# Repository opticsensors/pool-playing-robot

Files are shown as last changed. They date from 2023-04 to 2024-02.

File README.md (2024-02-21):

# `pool-paying-robot`

Design and implementation of a robot that plays the game of pool autonomously. To achieve this goal, three different branches had to be explored:
- **Vision system**: hardware and computer vision algorithms used for detecting and identifying pool balls
- **Shot selection**: algorithms to find the *best* shot given the balls configuration and pool table dimensions
- **Actuation system**: how to send commands to the actuators and the mechanical parts to make the execution of pool shots possible

## 1. Getting started

Run the following command for clonning the repository from GitHub:

```shell
git clone https://github.com/opticsensors/pool-playing-robot.git
```

Then:

1. Make sure  you have the latest version of pip and PyPA’s build installed:
   ```shell
   py -m pip install --upgrade pip
   py -m pip install --upgrade build
   ```

2. In your terminal, navigate to your new project, and initialise Git
   ```shell
   git init
   ```

3. Install the necessary packages using `pip`:
   ```shell
   py -m build
   py -m pip install -e .
   ```

4. Stage all your project files, and make your first commit
   ```shell
   git add .
   git commit -m "First commit"
   ```

## 2. Directory structure
The project follows this tree structure:

```
├── README.md                   <- The top-level README for developers using this project.
├── data                        <- Camera matrix, lens parameters, pool table corners, CNN weights ...
├── cad                         <- CAD files of the pool playing robot parts and the pool table. 
├── arduino                     <- Controls two stepper motors for positioning tasks, with options 
│                                  for homing, microstepping, and activating a solenoid.
│               
├── examples                    <- Python scripts.
│               
├── pyproject.toml              <- Makes project pip installable so src can be imported.               
│                                  The requirements are listed here.
│                
├── src                         <- Source code of this project.
│   └── pool            
│       └── __init__.py         <- Makes pool a Python module that can be imported from everywhere.
│       └── ball_detection.py   <- Computer vision algorithm for detecting pool balls.
│       └── brain.py            <- Analytic solution of 4 types of pool shots.
│       └── calibration.py      <- camera calibration and inverse kinematics of the robot.
│       └── cam.py              <- Controls a DSLR camera using digiCamControl's command line interface.
│       └── dynamixel.py        <- Interacts with the Dynamixel servomotors.
│       └── error_analysis.py   <- Finds the error due to the vision and actuation system
│       └── eye.py              <- Corrects camera lens distortion and adjusts the perspective. 
│       └── pool_env.py         <- Defines a custom environment for simulating a pool game.
│       └── pool_frame.py       <- Creates pool table dimansions and geometry
│       └── pool_sim.py         <- Simulates the physics of a pool game using the Pymunk library.
│       └── random_balls.py     <- Generates random pool ball positions.
│       └── shot_selection.py   <- Chooses what pool shot to play based on the ball positions.
│       └── stepper.py          <- Interacts with the Arduino to send commands to the stepper motors.
│       └── utils.py            <- Contains several system parameters and basic functions.
│
└── LICENSE.txt

```

## 3. Geometry of a pool shot

For the target ball `T` to pass through point `P`, the center of the pocket, the cue ball `C` must strike point `X`. 

Key measures:
- Cut angle: &gamma;
- Cue ball angle: &theta;
- Cue ball impact point: X 

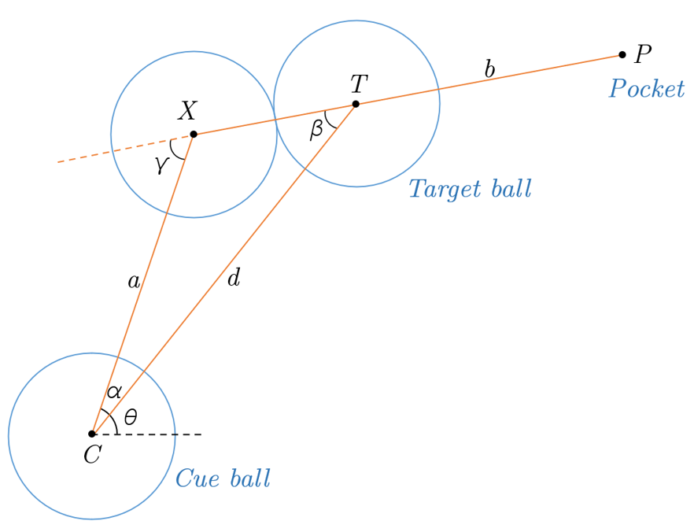
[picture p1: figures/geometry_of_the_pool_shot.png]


## 4. Error analysis

- **Objective**: determine the necessary resolution of the vision and actuation system
- **Simulation**: two ball cut shots that include a unique error via uniform sampling
- **Results**: analyze data with density plots to estimate success probability of sinking a ball

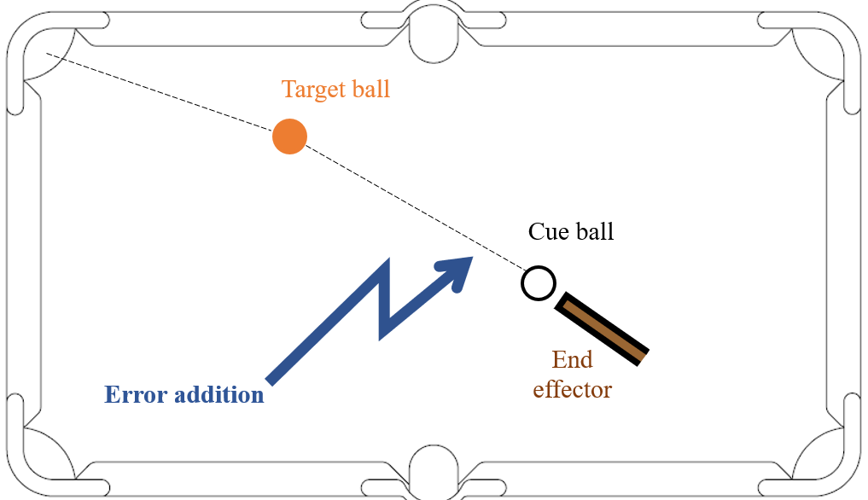
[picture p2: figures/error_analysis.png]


- **Actuation system**: the resolution is expressed as a range of angles from which the cue ball can be propelled. 

- **Vision system**: the resolution is defined by an uncertainty radius within which the predicted centers of the balls may vary. 

In both scenarios, the deviation of the target ball is quantified by the delta error (see image below):

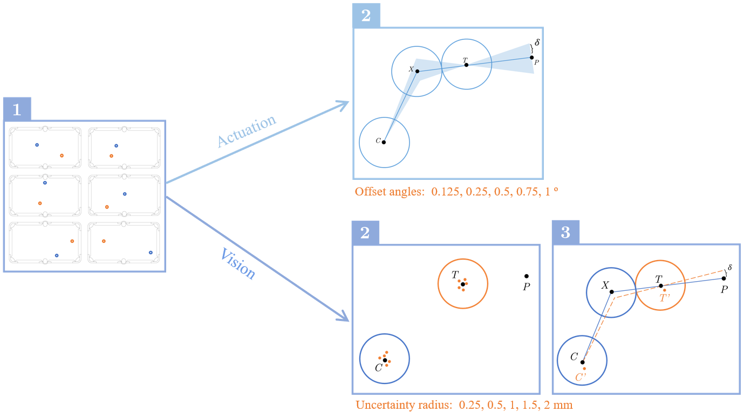
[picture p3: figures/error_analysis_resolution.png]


Analyzing the data from the simulation reveals that the cut angle has a significant effect on the delta error, particularly when this angle is bigger tha 60º, the error increases exponentially. This is why the density plots have been studied separately according to the cut angle.

<table>
  <tr>
    <th>Scatter plot</th>
    <th colspan="4">Density plot</th>
  </tr>
  <tr>
    <th>&delta; vs &gamma;</th>
    <th>0 ≤ γ ≤ 90 </th>
    <th>0 ≤ γ ≤ 30 </th>
    <th>30 ≤ γ ≤ 60</th>
    <th>60 ≤ γ ≤ 90</th>
  </tr>
  <tr>
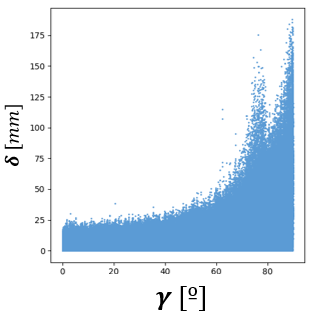
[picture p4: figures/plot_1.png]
    <td></td>
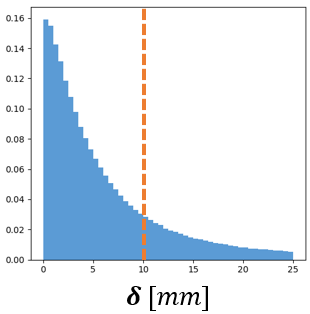
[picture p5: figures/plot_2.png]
    <td></td>
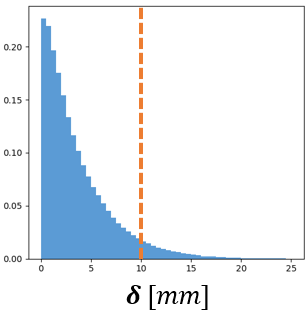
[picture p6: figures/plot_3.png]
    <td></td>
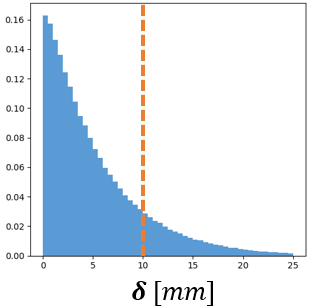
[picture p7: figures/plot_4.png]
    <td></td>
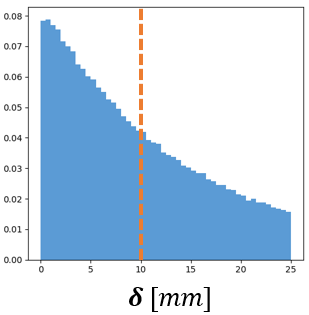
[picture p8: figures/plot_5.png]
    <td></td>
  </tr>
</table>

To calculate the probability of a ball being potted, one must compute the area under the curve of these diagrams between 0 and 10 mm of delta error, since the pockets approximately have a radius of 10 mm. Doing this for each of the resolutions studied, the results as a function of the cut angle are as shown in the tables. A glance at the probability values has led to the decision that the resolution of the vision system should be 0.5 mm or less, and that of the actuation system should be 0.25º or less.

<table>
  <tr>
    <th colspan="5">Probability results for different vision system resolutions </th>
  </tr>
  <tr>
    <th>Resolution</th>
    <th>0 ≤ γ ≤ 90</th>
    <th>0 ≤ γ ≤ 30</th>
    <th>30 ≤ γ ≤ 60</th>
    <th>60 ≤ γ ≤ 90</th>
  </tr>
  <tr>
    <td>0.25 mm</td>
    <td>0.86</td>
    <td>0.98</td>
    <td>0.93</td>
    <td>0.67</td>
  </tr>
  <tr>
    <td>0.5 mm</td>
    <td>0.80</td>
    <td>0.94</td>
    <td>0.84</td>
    <td>0.60</td>
  </tr>
  <tr>
    <td>1 mm</td>
    <td>0.73</td>
    <td>0.85</td>
    <td>0.75</td>
    <td>0.54</td>
  </tr>
  <tr>
    <td>1.5 mm</td>
    <td>0.68</td>
    <td>0.80</td>
    <td>0.69</td>
    <td>0.52</td>
  </tr>
  <tr>
    <td>2 mm</td>
    <td>0.66</td>
    <td>0.76</td>
    <td>0.65</td>
    <td>0.50</td>
  </tr>
</table>

<table>
  <tr>
    <th colspan="5">Probability results for different actuation system resolutions </th>
  </tr>
  <tr>
    <th>Resolution</th>
    <th>0 ≤ γ ≤ 90</th>
    <th>0 ≤ γ ≤ 30</th>
    <th>30 ≤ γ ≤ 60</th>
    <th>60 ≤ γ ≤ 90</th>
  </tr>
  <tr>
    <td>0.125°</td>
    <td>0.87</td>
    <td>0.99</td>
    <td>0.93</td>
    <td>0.66</td>
  </tr>
  <tr>
    <td>0.25°</td>
    <td>0.74</td>
    <td>0.87</td>
    <td>0.75</td>
    <td>0.58</td>
  </tr>
  <tr>
    <td>0.5°</td>
    <td>0.62</td>
    <td>0.72</td>
    <td>0.63</td>
    <td>0.45</td>
  </tr>
  <tr>
    <td>0.75°</td>
    <td>0.56</td>
    <td>0.62</td>
    <td>0.55</td>
    <td>0.45</td>
  </tr>
  <tr>
    <td>1°</td>
    <td>0.48</td>
    <td>0.53</td>
    <td>0.48</td>
    <td>0.38</td>
  </tr>
</table>

## 5. Vision system

### 5.1 Hardware

The hardware includes both the camera and its mounting support. The final setup is shown here:

| Top view | Side view |
|:---:|:---:|
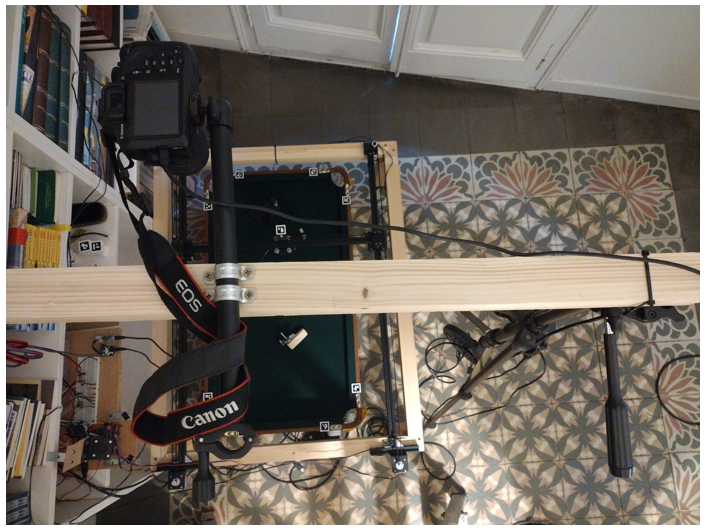
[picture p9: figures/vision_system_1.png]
Top view
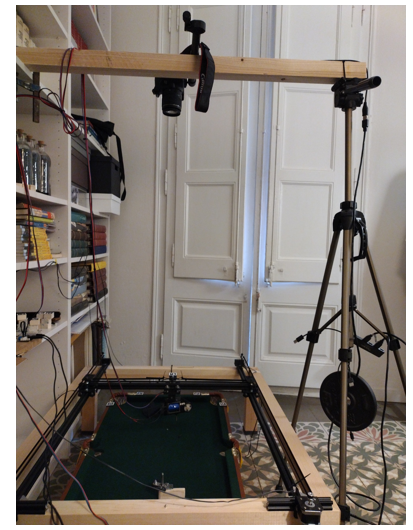
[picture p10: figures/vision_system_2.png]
Side view
|  |  |

To select the right camera, I conducted a resolution test on four different cameras I had at home: a smartphone camera, a Raspberry Pi camera, a DSLR, and a webcam. Based on the results and ease of connectivity with a PC, the final selection was the DSLR camera:

<table>
  <tr>
    <th>Camera</th>
    <td>Samsing A71</td>
    <td>PiCamera</td>
    <td>Canon EOS 1300D</td>
    <td>Logitech c922</td>
  </tr>

  <tr>
    <th>Resolution</th>
    <td>0.28 mm/px</td>
    <td>0.50 mm/px</td>
    <td>0.25 mm/px</td>
    <td>0.50 mm/px</td>
  </tr>

  <tr>
    <th>USAF test</th>
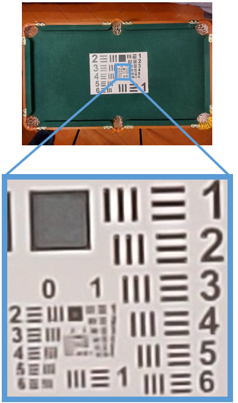
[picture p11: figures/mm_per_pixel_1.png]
    <td>
</td>
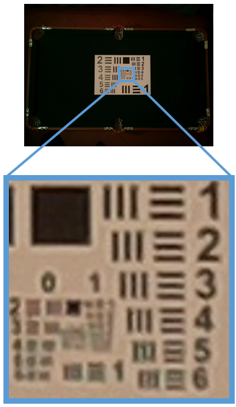
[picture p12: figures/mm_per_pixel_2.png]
    <td>
</td>
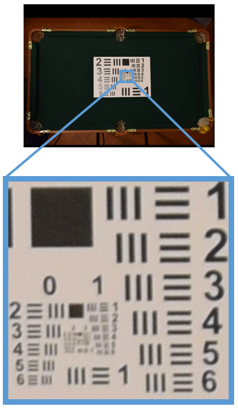
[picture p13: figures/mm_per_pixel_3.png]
    <td>
</td>
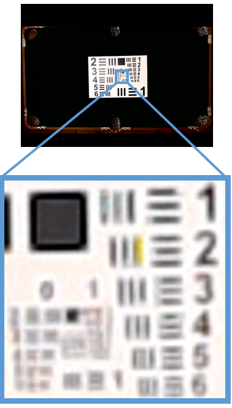
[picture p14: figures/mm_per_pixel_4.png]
    <td>
</td>
  </tr>

</table>

### 5.2 Software

#### 5.2.1 Preprocessing

- **Lens correction**: prevents straight lines from appearing curved.

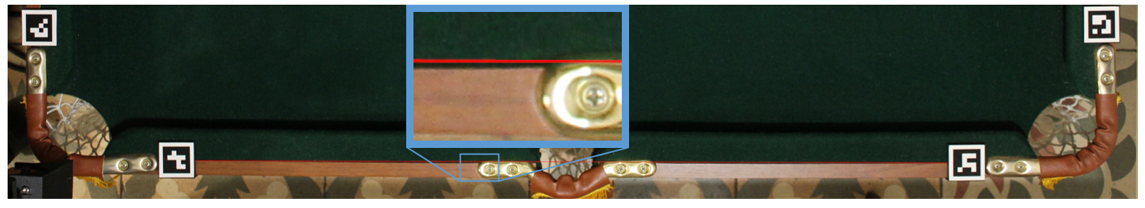
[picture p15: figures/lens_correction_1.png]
| **Before** |  |
|---|---|
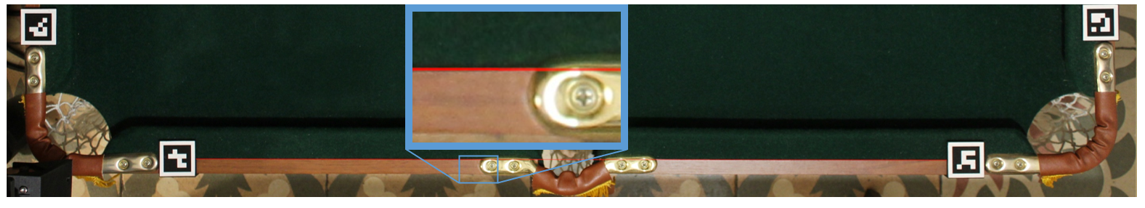
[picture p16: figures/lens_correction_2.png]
| **After** |  |

- **Homography**: Transforms the image so that its corners align with those of the pool table.

| Before | After |
|---|---|
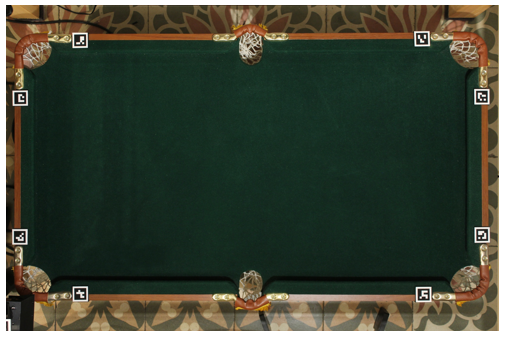
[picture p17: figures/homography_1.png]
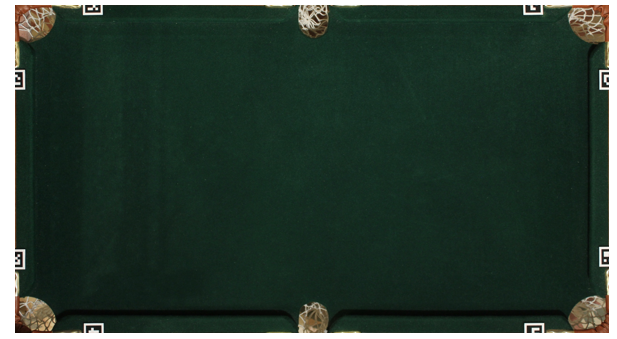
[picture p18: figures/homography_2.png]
|  |  |

- **Camera calibration**: Computes the intrinsic camera parameters using images of a checkerborad pattern.

| Image 1 | Image 2 | Image 3 | Image 4 |
|:-----:|:-----:|:---:|:---:|
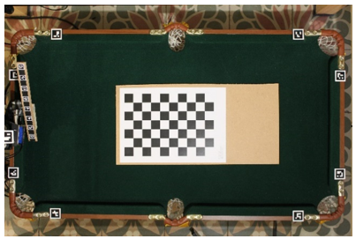
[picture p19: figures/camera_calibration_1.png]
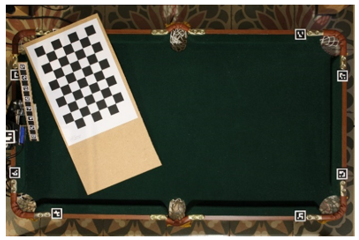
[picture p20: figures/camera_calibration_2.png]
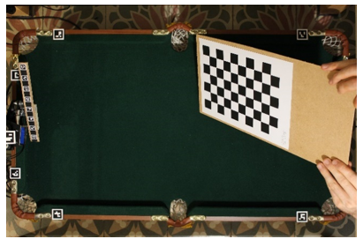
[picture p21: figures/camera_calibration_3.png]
|  |  |  | [...]

#### 5.2.2 YOLOv8

This approach uses the YOLO (version 8 by Ultralytics) detection algorithm, where the image is processed through a CNN, resulting in predictions in the form of rectangles.

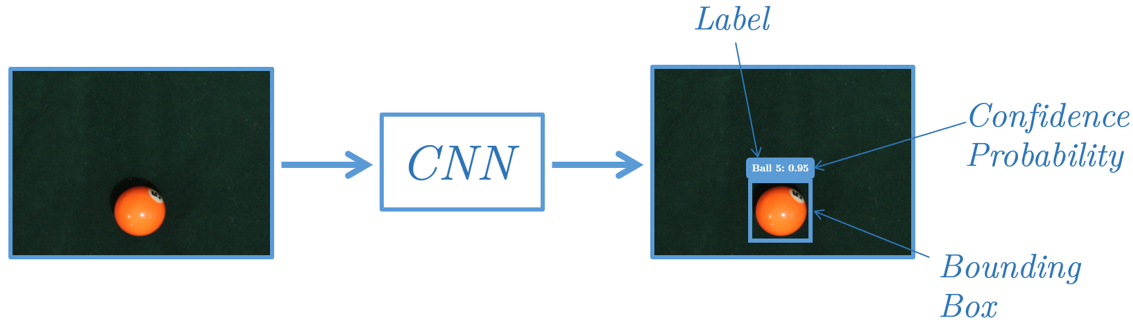
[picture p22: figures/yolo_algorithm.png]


#### 5.2.3 Classic approach

This method employs a set of classic computer vision techniques: color segmentation, morphological operations, the watershed algorithm and color transformation. 

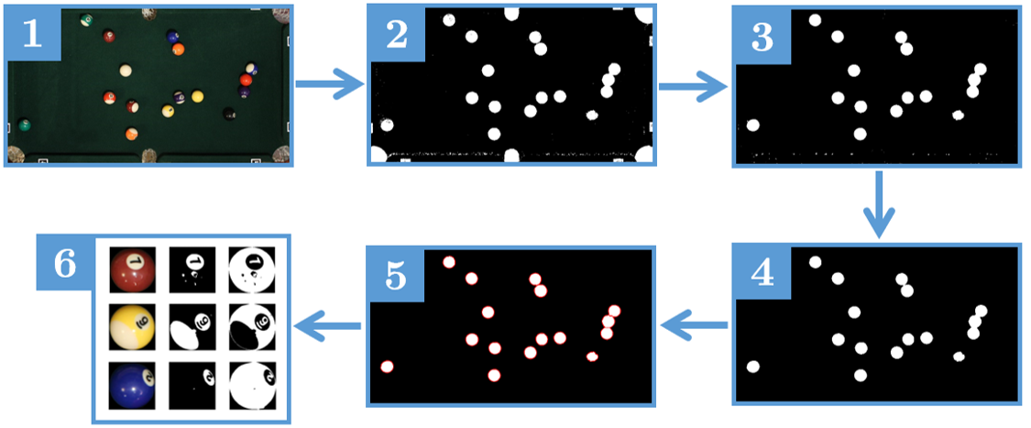
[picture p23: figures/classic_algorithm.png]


#### 5.2.4 Comparison of the results

After comparing the results of both methods against a Ground Truth established by me, it was observed that the classic method is more accurate, but less robust in situations where the balls are very close to each other. 

| Original | Ground truth | Classic | YOLOv8 |
|---|---|---|---|
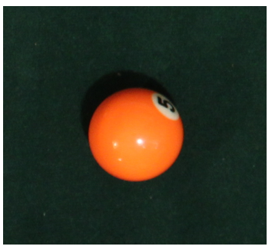
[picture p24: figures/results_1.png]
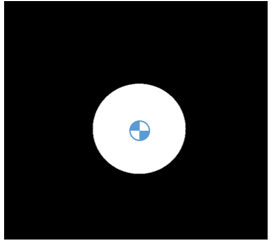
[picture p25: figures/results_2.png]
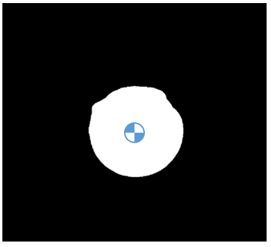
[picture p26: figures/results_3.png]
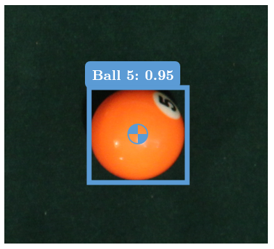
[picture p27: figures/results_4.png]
YOLOv8
|  |  |  |  |

| Algorithm | &mu; [px] | &sigma; [px] |
|---|---|---|
| YOLO | 3.02 | 3.17 |
| Classic | 2.43 | 1.81 |

If the 68–95–99.7 rule is applied, from these results it can be deduced that in 95% of the cases an error below 6.3 and 3.6 pixels should be expected for the YOLO and classic algorithms, respectively. Considering a resolution of 0.25 mm/px, this is 1.5 and 0.9 mm, respectively.

<details><summary><b>Results</b></summary>

Detection of pool balls grouped closely together

| Classic | YOLO |
|---|---|
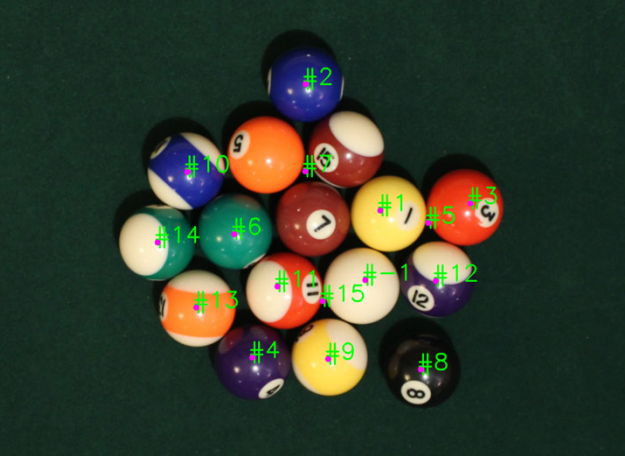
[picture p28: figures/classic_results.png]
Classic
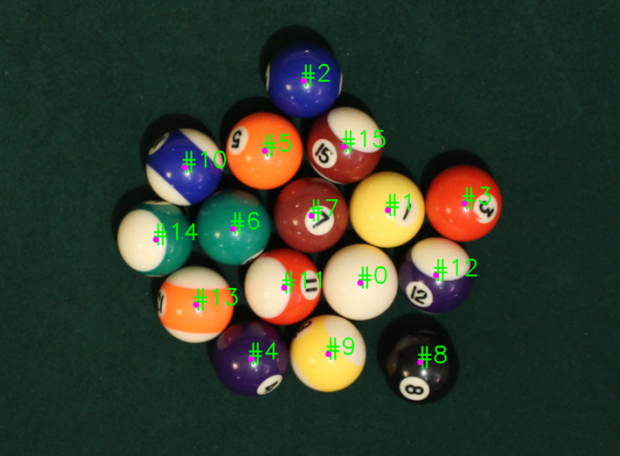
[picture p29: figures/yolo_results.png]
YOLO
|  |  |

</details>

## 6. Shot selection 

### 6.1 Analytic method

- **Pool table geometry simplification**: to simplify the computation of rebounds.

| Original | Simplified |
|---|---|
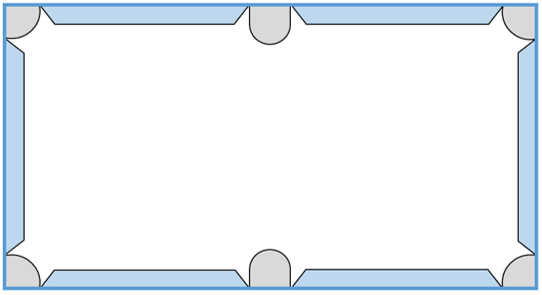
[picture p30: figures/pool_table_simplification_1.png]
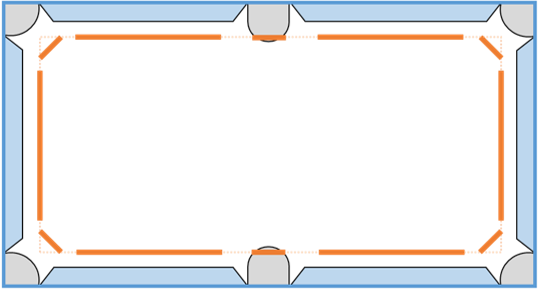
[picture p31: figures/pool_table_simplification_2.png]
|  |  |

- **Compute all possible and impossible shots**: combinations of all the different balls and pockets.

| CTP | CTTP | CBTP | CTBP |
|---|---|---|---|
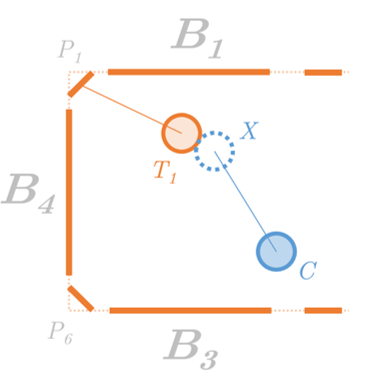
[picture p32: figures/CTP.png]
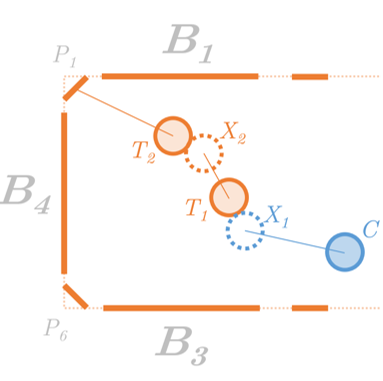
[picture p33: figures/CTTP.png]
CTTP
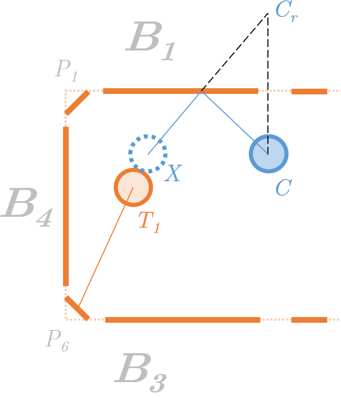
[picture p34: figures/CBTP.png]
CBTP
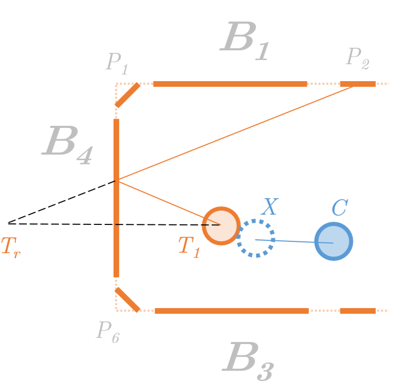
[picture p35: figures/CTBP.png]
CTBP
|  |  |  |  |

- **Filter feasible shots**: collision check using the geometric definition of the cross and dot products.

| No collision | Collision |
|:---:|:---:|
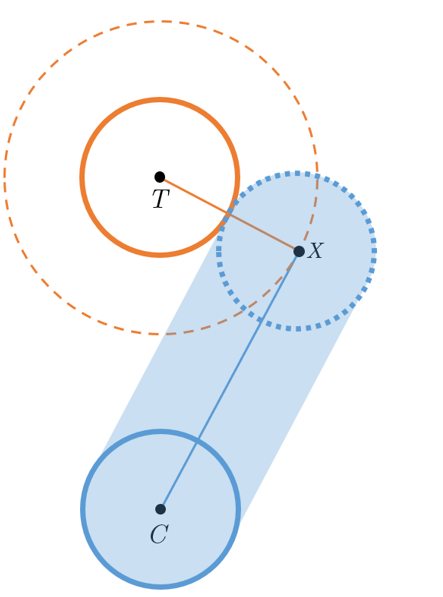
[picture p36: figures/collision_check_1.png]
No collision
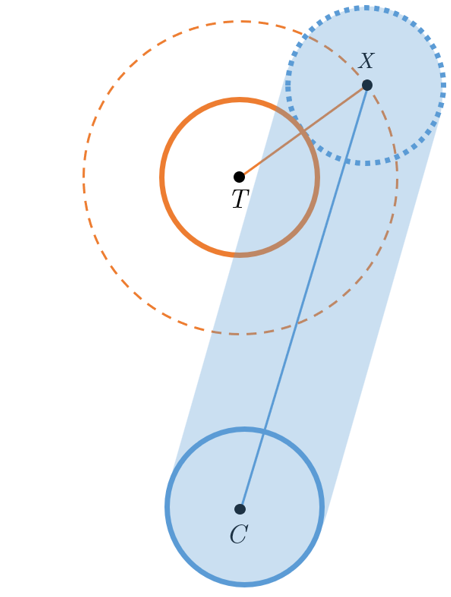
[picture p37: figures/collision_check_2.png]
Collision
|  |  |

- **Choosing the easiest shot**: difficulty metric (using the nomenclature defined above)

$$
\text{difficulty} = \frac{ab}{\cos^2 \gamma}
$$

<details><summary><b>Results</b></summary>

| CTP | CTTP | CBTP | CTBP |
|---|---|---|---|
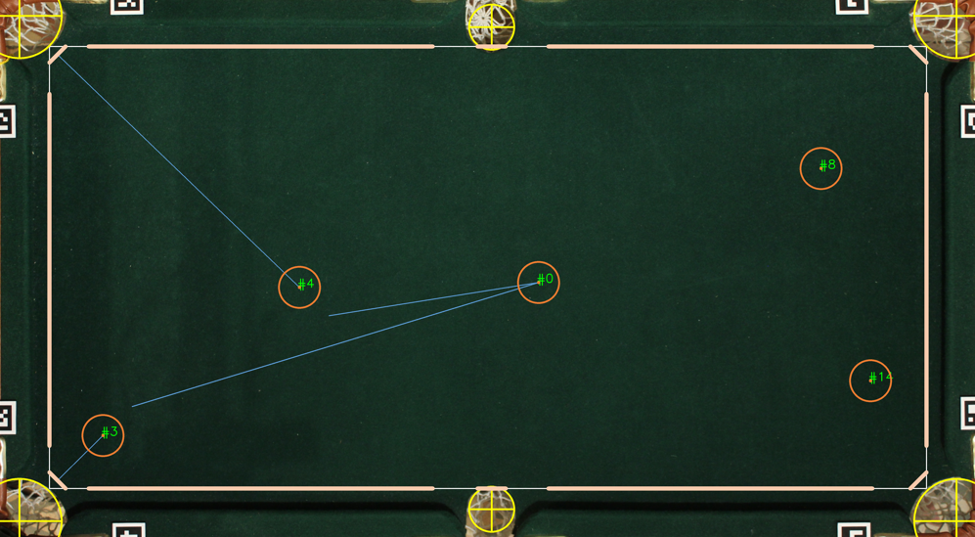
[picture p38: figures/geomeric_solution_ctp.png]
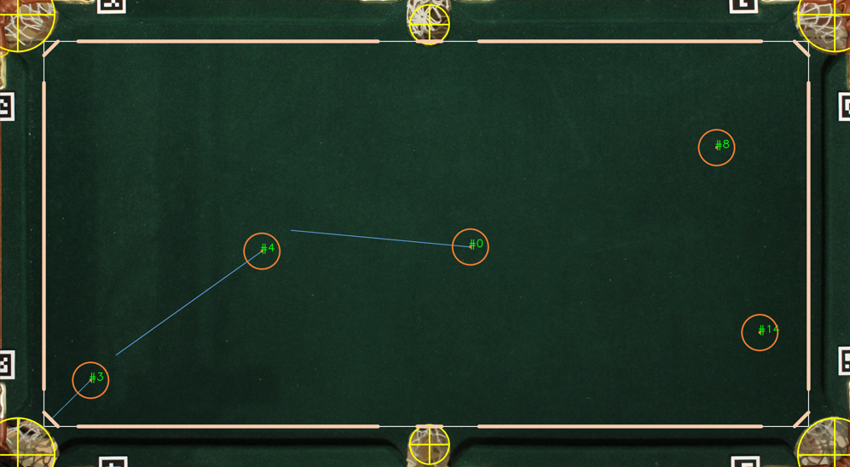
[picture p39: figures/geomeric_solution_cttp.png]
CTTP
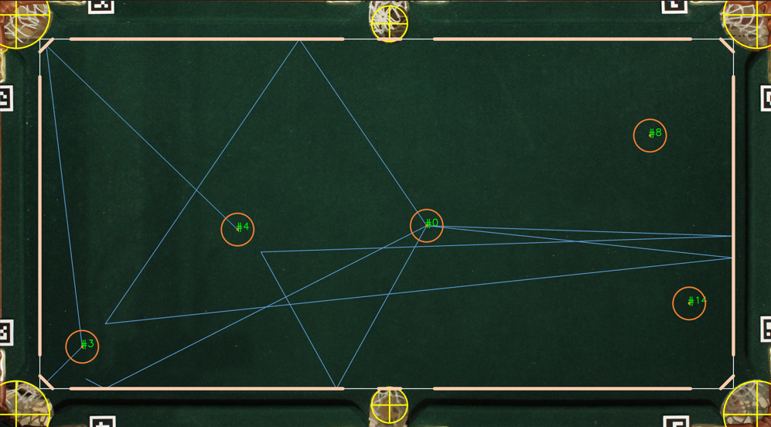
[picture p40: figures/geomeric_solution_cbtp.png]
CBTP
|  |  |  | CTBP |

</details>

### 6.2 Simulation method

- **2D simulation & render**: Pymunk, Pygame
- **Brute force**: every angle is simulated (incr. 0.1º)
- **Easiest shot**: less sensitive angle



## 7. Actuation system: 

The pool robot is divided in 2 subsystems:

- **Cue ball impact**: linear actuator
   - Solenoid
   - Servomotor
- **Cue positioning**: cartesian robot
   - Stepper motors
   - V-slot 2020 and wheels
   - Tooth belt and timing pulleys 

Block diagram of the actuation system showing selected components and
interactions:



- **Homing position**: it's necessary to have a reference position known as home since the stepper motors do not have a way to know their position. This position has been obtained using two limit switches activated by the robot's own moving parts:

<table>
  <tr>
    <th>SolidWorks</th>
    <th>Constructed</th>
  </tr>
  <tr>
    <td rowspan="2">SolidWorks
</td>
    <td>Constructed</td>
  </tr>
  <tr>
    <td>Constructed</td>
  </tr>
</table>

- **Timing belt and pulleys**: the belt has been designed with an H configuration which has allowed the motors to be stationary

<table>
  <tr>
    <th>Concept design H-bot</th>
    <th>Constructed</th>
  </tr>
  <tr>
    <td rowspan="2">SolidWorks
</td>
    <td>Constructed</td>
  </tr>
  <tr>
    <td>Constructed</td>
  </tr>
</table>

- **Belt tensioning and stepper sizing**: a set of pulleys was assembled and the belt was tensioned with zip ties. To achieve this the motors were sized with a calculation of the required torque, considering the accelaration and load terms, and a safety factor

| Belt tensioning | Stepper mount |
|---|---|
| Before | After |

### 7.1 Fliper design:

- **Why a flipper mechanism was developed?**: Because it requires one less degree of freedom, hence, on less motor.

| 2 DOF | 1 DOF |
|:---:|:---:|
| 2 DOF | 1 DOF |

- **Iterative design process**: The first iteration was entirely made with 3D-printed parts and served to test the viability of the concept. This proved successful, leading to a second iteration where the piece was modified to integrate a component from a pinball machine, in order to make it more robust. The final step involved rotating the flipper relative to the Cartesian robot's carriage. To accomplish this, a servo motor was coupled between the two parts.

| Proof of concept | Pinball parts | Servo integration |
|:-----:|:-----:|:---:|
| 2 DOF | 2 DOF | 2 DOF |

- **Solenoid stroke and spring**:  the solenoid's stroke was limited using a screw, and the flipper's return to the retracted position was achieved with a spring.

Stroke                       |            Spring
:-------------------------:|:-------------------------:
|  

### 7.2 Flipper parts:

- **Linkage kinematics simulation**: to obtain the dimensions of the mechanism, its kinematics have been simulated for many possible configurations, and the one that met a series of requirements was selected. For example, ensuring that the flipper, when retracted, does not collide with any balls that might be on the table.

- **Flipper assembly**: to secure the wooden flipper to the steel shaft, Araldite was used, while the shaft was joined to the metal part through welding. 

Flipper assembly           |            Flipper parts
:-------------------------:|:-------------------------:
|  

### 7.3 Control and communications: 

- **Stepper motor**:
   - Accelstepper library
   - Pulse control: steps and direction
   - Stepper driver: DRV8825
   
- **Servomotor**:
   - Dynamixel library: address writing 
   - Trapezoidal velocity profile
   - PID angular position

- **Solenoid**:
   - Logic MOSFET circuit

- **PC interface**:
   - Arduino: serial communication 
   - USB communication converter 

### 7.4 Final prototype:

The cartesian robot is supported by a wooden frame, and the flipper is held in place thanks to the sliding wheel element of the central bar, which is inverted.

SolidWorks                      |            Constructed
:-------------------------:|:-------------------------:
|  

## 8. System integration

Find relationship between:

- Outputs from the vision system: cue ball pixel coordinates `uc`, `vc`
- Outputs from the shot selection algorithm: cue ball trajectory angle &theta;
- Commands to be sent to the stepper motors: `q1`, `q2`; and the servomotor: `q3`

### 8.1 Robot kinematics

- **Cartesian robot kinematics**: relationship between the stepper motors' rotational movement and the linear displacement of the carriage. 

Stepper rotation vs. carriage movement   |            Steps vs. distance
:-------------------------:|:-------------------------:
|  

- **Evaluating flipper positioning**: The flipper has an offset relative to the axis of rotation.

| Initial condition | Flipper rotation | Flipper translation |
|:-----:|:-----:|:---:|
| Initial condition | Flipper rotation | Flipper translation |

It was deduced that:

- The cue ball's position in pixels (`uc`, `vc`), and the cosine and sine of the flipper's angle (&theta;), have a linear relationship with the steps of the motors (`q1`, `q2`). 

- The flipper's angle (&theta;) directly corresponds to the position we need to set the servo motor to (`q3`).

### 8.2 Calibration procedure

A calibration process was developed to experimentally determine the robot's inverse. This process involves:

1. Move the carriage to six predetermined known positions. 
2. For each of these positions, the servo motor must be moved to a random angle.
3. Place an Aruco marker directly under the flipper, simulating where the cue ball would be located.

| Predefined grid of points | Aruco under the flipper  | Final Aruco positions |
|:-----:|:-----:|:---:|
| Predefined grid of points | Aruco under the flipper | Final Aruco positions |

By using the information from the Aruco markers' positions (`uc`, `vc`), as well as the positions of the carriage and the servo motor (`X_C`, `Y_C`, &theta;), a dataset can be created. This dataset allows for the adjustment of a linear regression model between the desired variables.

$$
X_c = A \cos \theta + B \sin \theta + C u_c + D v_c + E
$$

$$
Y_c = F \cos \theta + G \sin \theta + H u_c + I v_c + J
$$

After computing the linear regression coefficients, the required motor steps can be determined via the inverse kinematics:

$$
\begin{bmatrix} q_1 \\\ q_2 \end{bmatrix} = 1/\lambda \begin{bmatrix} -1/2 & 1/2\\\ 1/2 & 1/2\end{bmatrix} \begin{bmatrix} X_C \\\ Y_C \end{bmatrix}
$$

## 9. Results 

20 cut shots (for cut angle less than 45º):
 - 15 out of 20 successful shots (75% success rate)
 - Cue ball trajectory: 
   - Average deviation of 0.65º
   - Standard deviation of 0.4º (max deviation of 1.2º)

| Shot 1 |  Shot 2 |  Shot 3 |  Shot 4 |
|---|---|---|---|
| Shot 1 | Shot 2 | Shot 3 | Shot 4 |

The results were obtained using video analysis of the cue ball trajectory:
- Camera: smartphone top down view
- Ball tracking: MOG
- Cue path angle: GIMP

Top down view                      |            MOG results
:-------------------------:|:-------------------------:
|

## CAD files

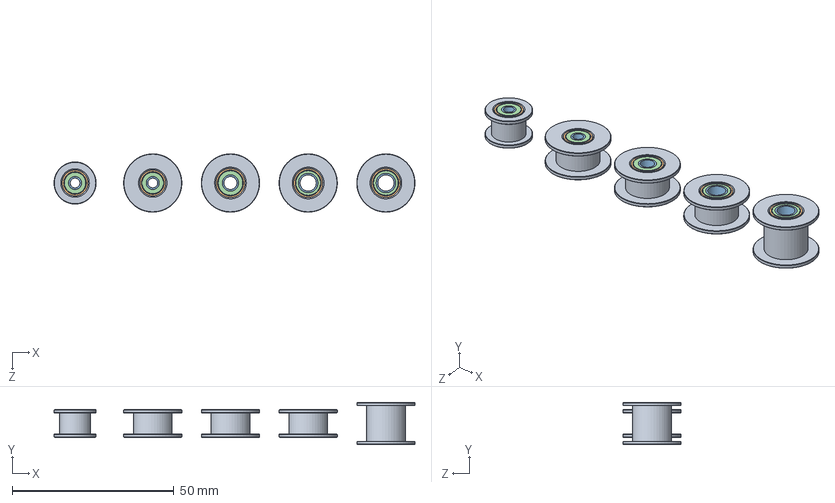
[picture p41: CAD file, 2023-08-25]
cad/solid_works/GT2 Idler Pulley, Configurable, Pulleys Lined Up in Assembly.SLDASM
111.5 x 13.0 x 18.0 mm
Body, GT2 Idler Pulley, Configurable x 5
Bearing Outer Ring, GT2 Idler Pulley, Configurable x 10
Bearing Inner Ring, GT2 Idler Pulley, Configurable x 10
Bearing Seal, GT2 Idler Pulley, Configurable x 20
Bearing Ball, GT2 Idler Pulley, Configurable x 88

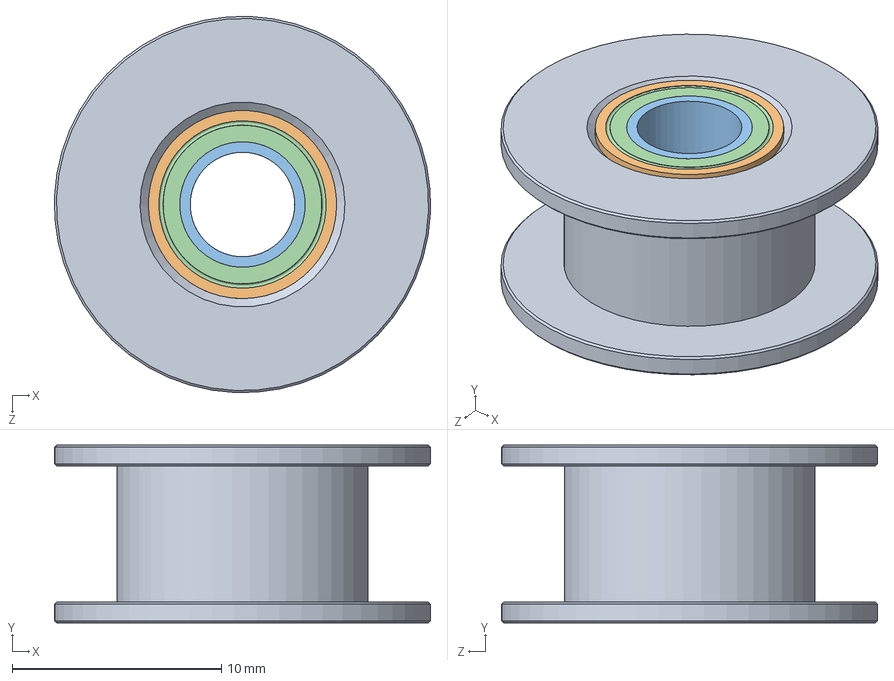
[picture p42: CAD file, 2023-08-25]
cad/solid_works/GT2 Idler Pulley, Configurable.SLDASM
18.0 x 8.50 x 18.0 mm
Body, GT2 Idler Pulley, Configurable
Bearing Outer Ring, GT2 Idler Pulley, Configurable x 2
Bearing Inner Ring, GT2 Idler Pulley, Configurable x 2
Bearing Seal, GT2 Idler Pulley, Configurable x 4
Bearing Ball, GT2 Idler Pulley, Configurable x 24

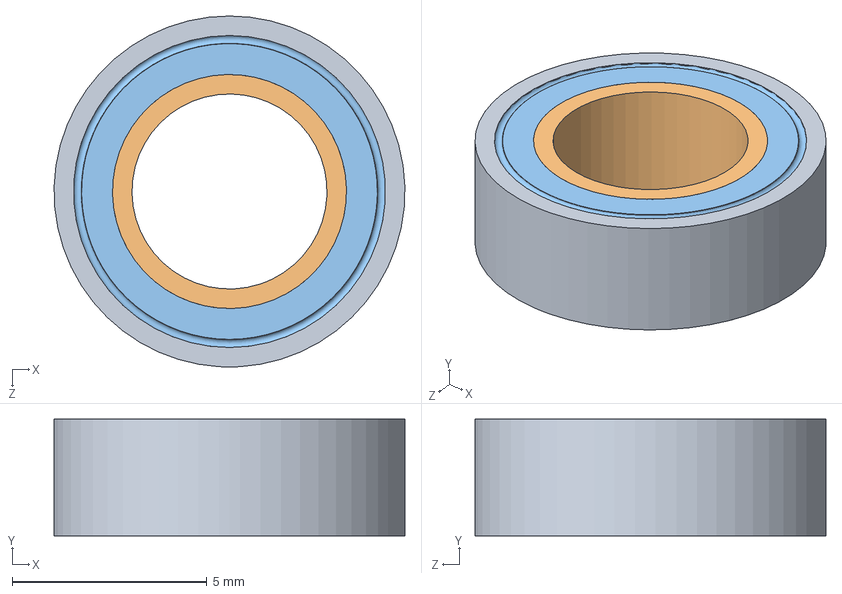
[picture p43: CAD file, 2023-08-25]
cad/solid_works/Bearing Subassy, GT2 Idler Pulley, Configurable.SLDASM
9.00 x 3.00 x 9.00 mm
Bearing Outer Ring, GT2 Idler Pulley, Configurable
Bearing Inner Ring, GT2 Idler Pulley, Configurable
Bearing Seal, GT2 Idler Pulley, Configurable x 2
Bearing Ball, GT2 Idler Pulley, Configurable x 12

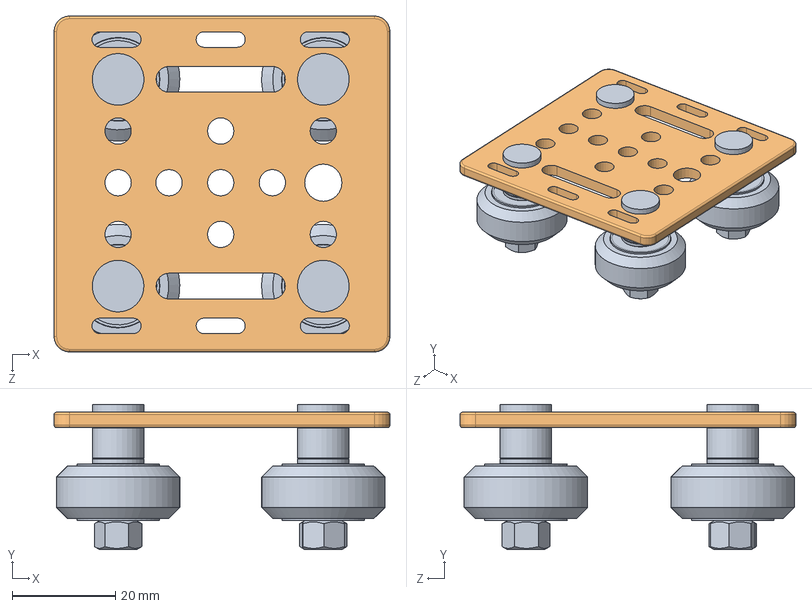
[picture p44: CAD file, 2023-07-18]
cad/solid_works/v wheels + plate.SLDASM
65.0 x 28.1 x 65.0 mm
v wheel x 4
v wheel plate v2

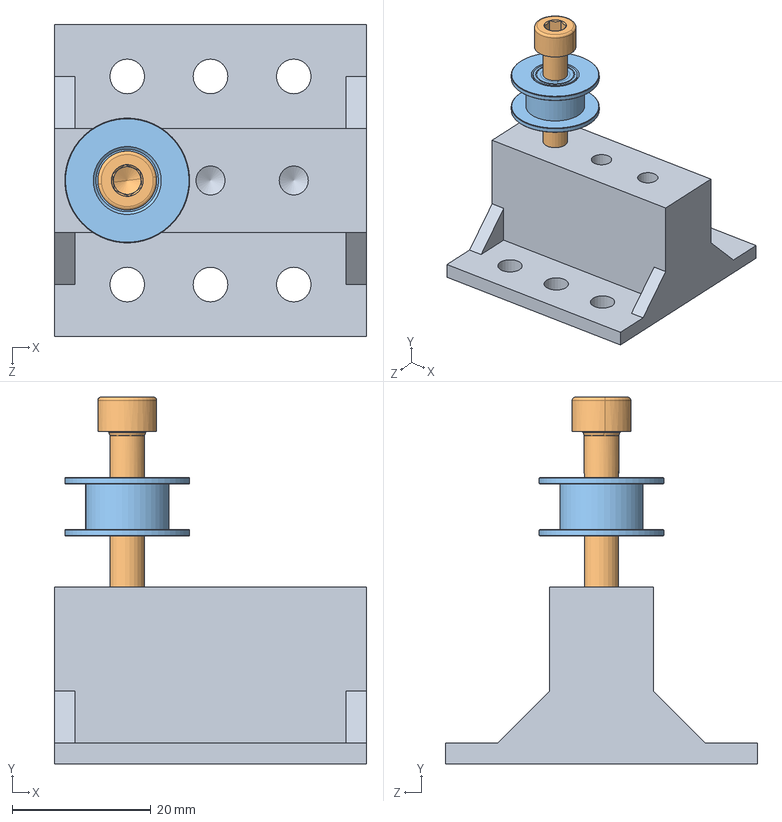
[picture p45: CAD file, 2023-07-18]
cad/solid_works/single idler pulley support.SLDASM
45.0 x 52.9 x 45.0 mm
single idler pulley support
m5 allen screw 40mm
GT2 Idler Pulley

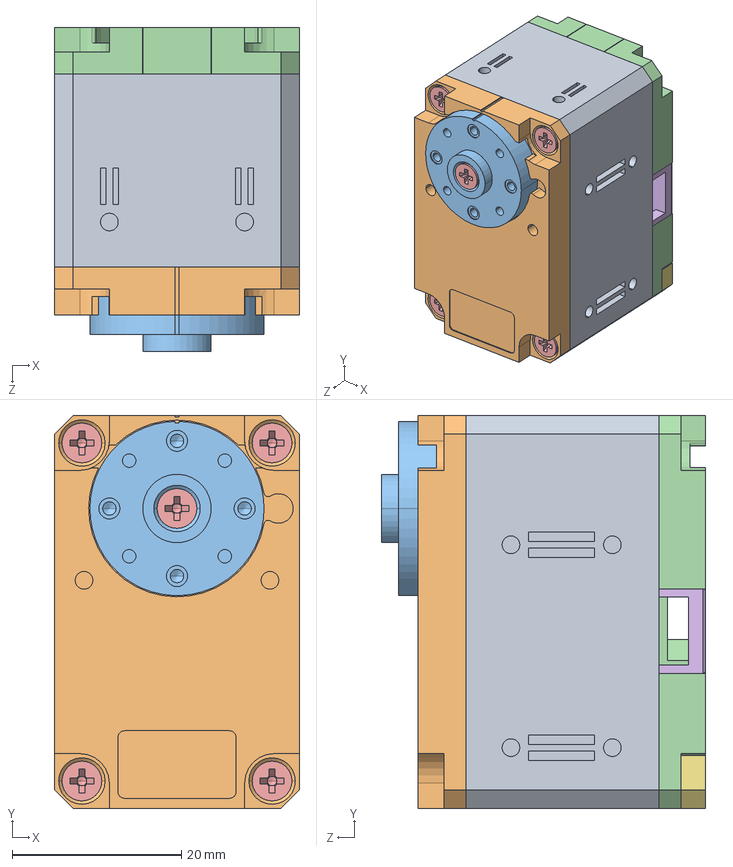
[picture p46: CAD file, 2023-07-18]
cad/solid_works/XL430_W250_T.SLDASM
29.0 x 46.5 x 38.3 mm
Part1^XL430_W250_T.STEP
Part2^XL430_W250_T.STEP
Part3^XL430_W250_T.STEP
Part4^XL430_W250_T.STEP
countersunk flat head cross recess screw_din_DIN EN ISO 7046-1 - M2.5 x 10 - Z - 10N.STEP x 9
Part5^XL430_W250_T.STEP
Part6^XL430_W250_T.STEP

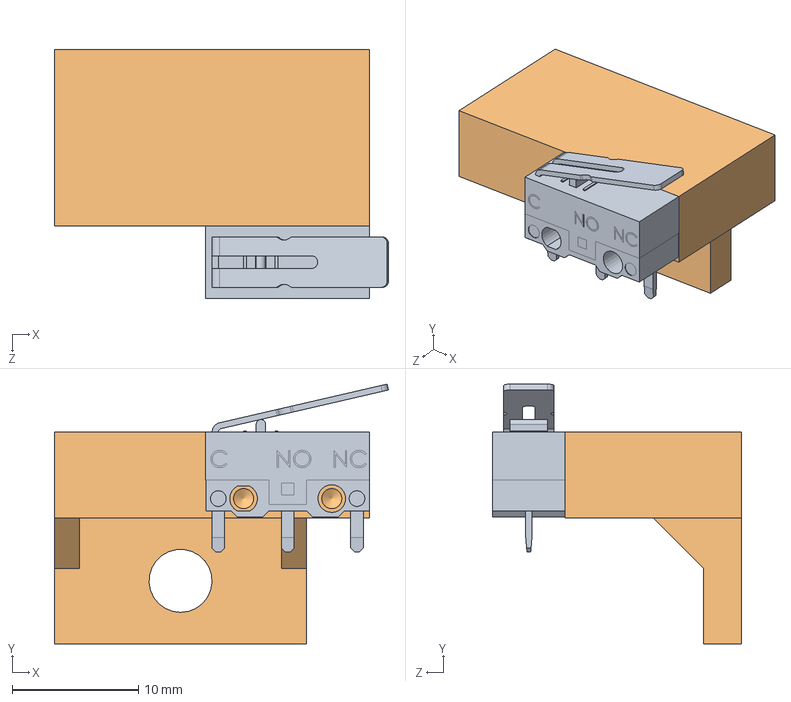
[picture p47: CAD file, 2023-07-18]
cad/solid_works/Limit_Switch_assembly.SLDASM
26.5 x 20.6 x 19.8 mm
Limit_Switch
limit_switch_support v3

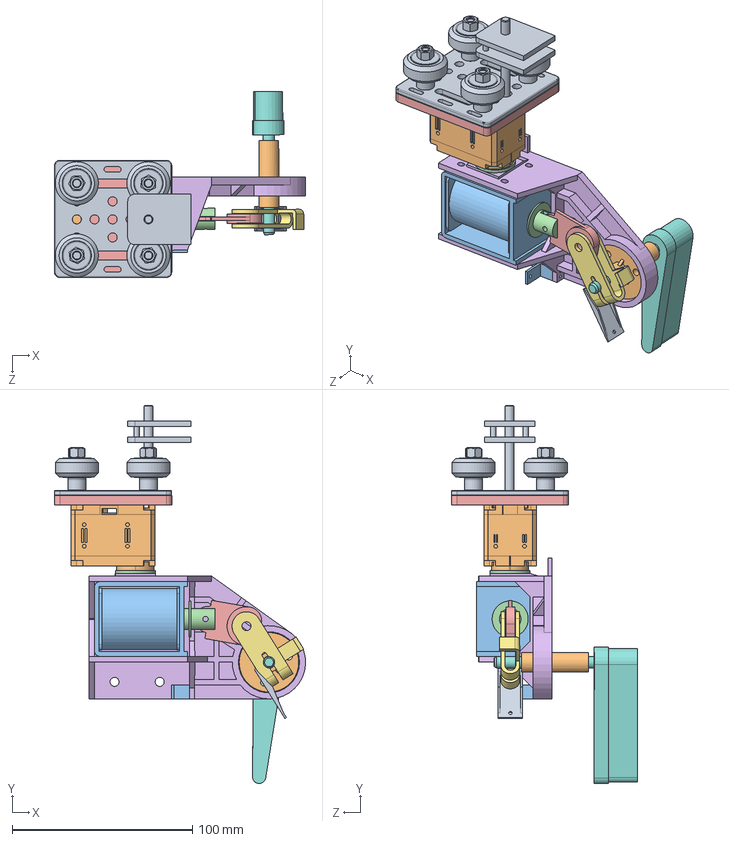
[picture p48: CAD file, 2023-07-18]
cad/solid_works/Actuator.SLDASM
139.2 x 209.5 x 103.1 mm
v wheels + plate central
XL430_W250_T
Heshchen_solenoid
Heshchen_plungger
l1_link
case x 2
l2_link_v2
flipper
tensioner_holder
axis_support
spring_holdder
dynamixel_spacer
dynamixel_support

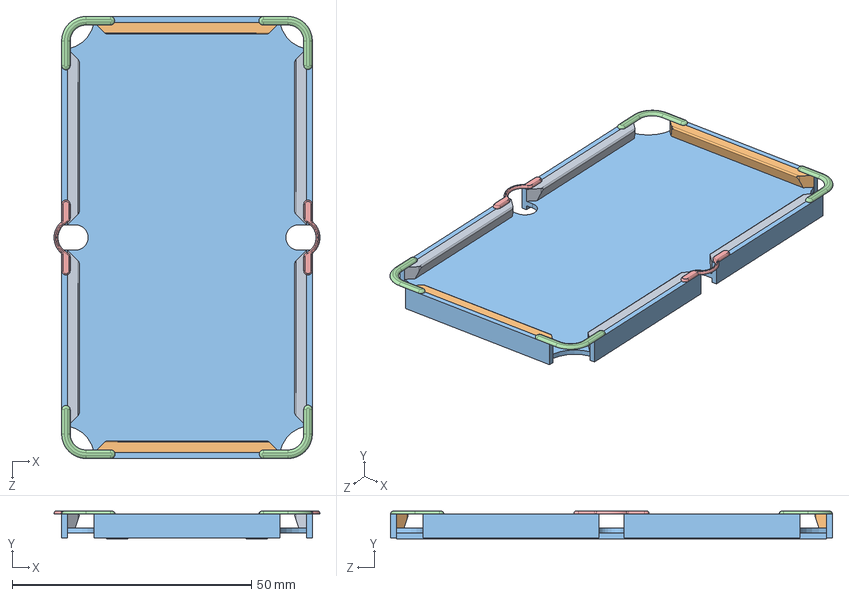
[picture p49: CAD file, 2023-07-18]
cad/solid_works/billar.SLDASM
55.6 x 5.84 x 92.4 mm
borde_corto x 4
borde_largo x 2
mesa
corner_strap x 4
middle_straps x 2

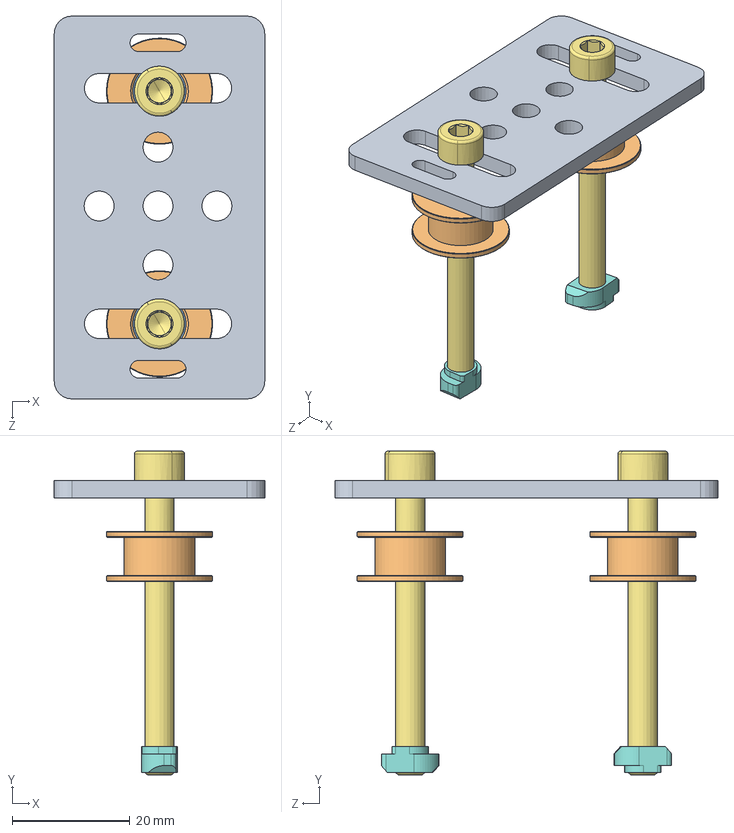
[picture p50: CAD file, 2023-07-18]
cad/solid_works/idler pulley support.SLDASM
35.7 x 55.0 x 65.0 mm
idler pulley plate
Body, GT2 Idler Pulley, Configurable x 2
Bearing Outer Ring, GT2 Idler Pulley, Configurable x 4
Bearing Inner Ring, GT2 Idler Pulley, Configurable x 4
Bearing Seal, GT2 Idler Pulley, Configurable x 8
Bearing Ball, GT2 Idler Pulley, Configurable x 48
m5 allen screw x 2
M5_T_Slot nut x 2

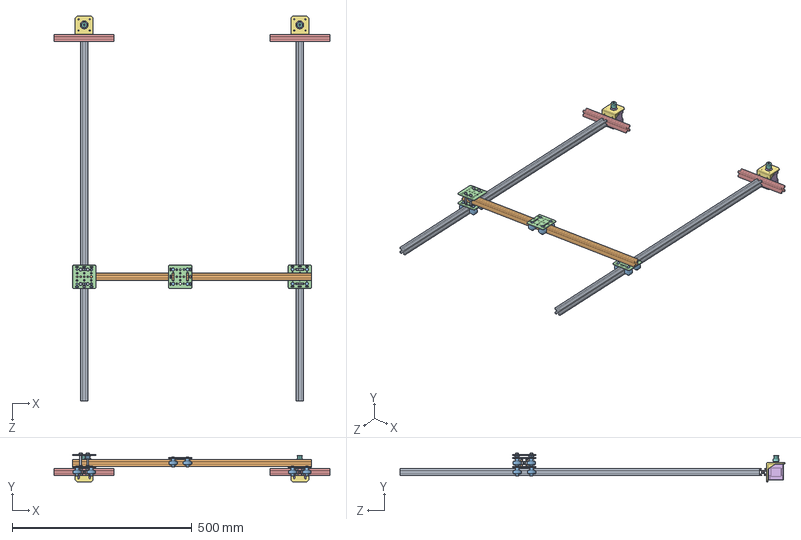
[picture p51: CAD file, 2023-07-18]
cad/solid_works/cartesian_robot.SLDASM
767.0 x 80.4 x 1071.5 mm
v slot 2020 1000mm x 2
v slot 2020 666mm
v wheel x 12
v wheel plate x 4
v slot 2020 167mm x 2
NEMA 17 x 2
Stepper Motor Mount NEMA_17 Sized x 2
2GT 20B5 x 2
formed hex screw_am x 4
hex nut jam_am x 4
GT2 Timing Idler Pulley x 2

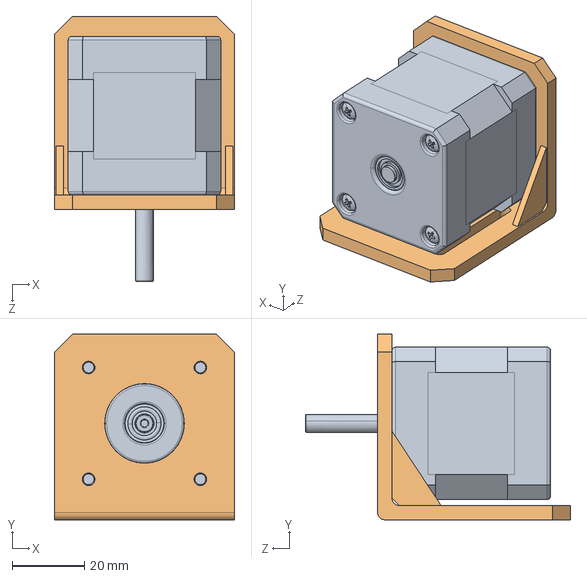
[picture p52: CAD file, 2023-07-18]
cad/solid_works/NEMA 17 + support.SLDASM
50.0 x 51.5 x 73.5 mm
NEMA 17
Stepper Motor Mount NEMA_17 Sized

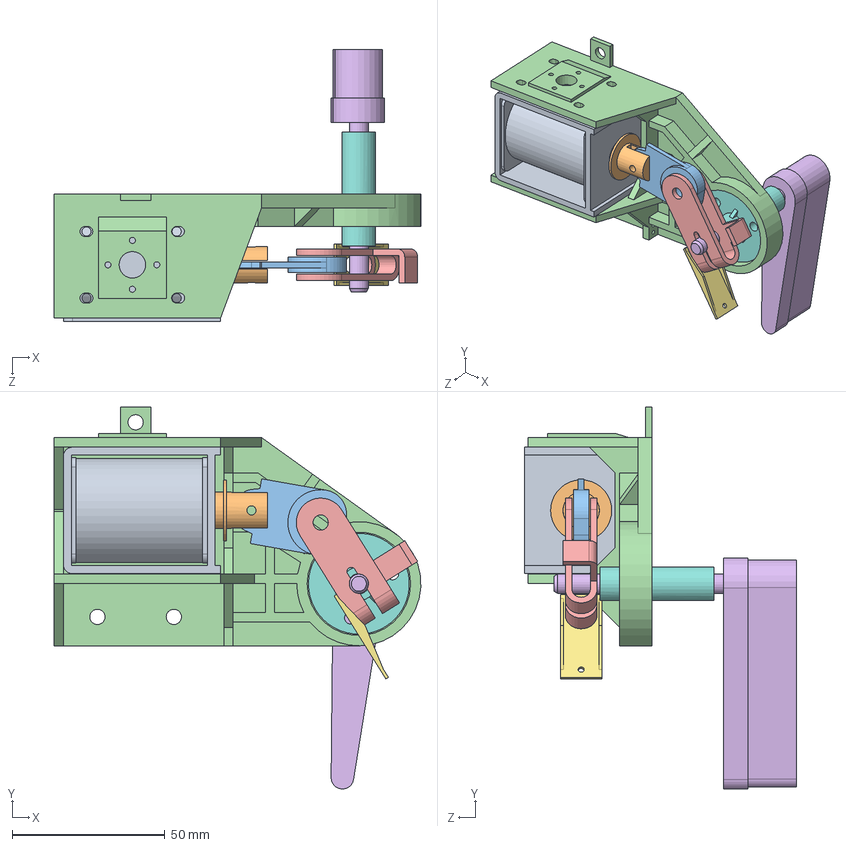
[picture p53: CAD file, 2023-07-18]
cad/solid_works/my_pinball_flipper_design.SLDASM
120.0 x 125.0 x 89.1 mm
Heshchen_solenoid
Heshchen_plungger
l1_link
case
l2_link_v2
flipper
tensioner_holder
axis_support

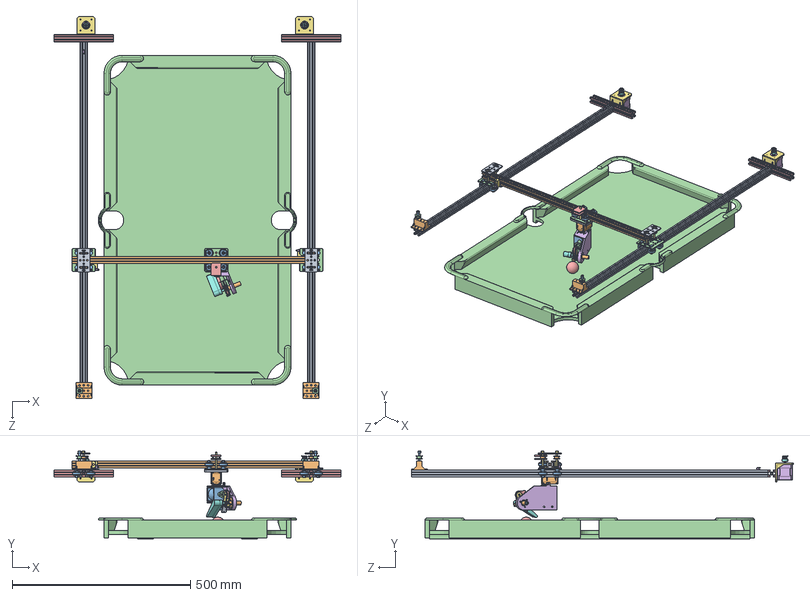
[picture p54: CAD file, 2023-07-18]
cad/solid_works/my final design.SLDASM
804.0 x 246.1 x 1071.5 mm
v slot 2020 1000mm x 2
v slot 2020 666mm
v wheel x 12
v wheel plate v2 x 3
v slot 2020 167mm x 2
NEMA 17 x 2
Stepper Motor Mount NEMA_17 Sized x 2
2GT 20B5 x 2
idler pulley plate x 4
Body, GT2 Idler Pulley, Configurable x 8
Bearing Outer Ring, GT2 Idler Pulley, Configurable x 16
Bearing Inner Ring, GT2 Idler Pulley, Configurable x 16
Bearing Seal, GT2 Idler Pulley, Configurable x 32
Bearing Ball, GT2 Idler Pulley, Configurable x 192
m5 allen screw x 9
M5_T_Slot nut x 8
hex nut style 1_am x 8
single idler pulley support x 4
m5 allen screw 40mm x 4
GT2 Idler Pulley x 4
belt tensioner
Limit_Switch x 3
limit_switch_support v3 x 2
dynamixel_spacer
dynamixel_support
XL430_W250_T
Heshchen_solenoid
Heshchen_plungger
l1_link
case
l2_link_v2
flipper
tensioner_holder
axis_support
spring_holdder
billar scaled
bola

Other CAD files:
cad/solid_works/SimetríaLimit_Switch_assembly.SLDASM
cad/solid_works/GT2 Idler Pulley.SLDASM
cad/solid_works/v wheels + plate central.SLDASM
cad/solid_works/cartesian_robot v4.SLDASM
cad/solid_works/2GT 20B5.SLDPRT
cad/solid_works/Bearing Ball, GT2 Idler Pulley, Configurable.SLDPRT
cad/solid_works/Bearing Inner Ring, GT2 Idler Pulley, Configurable.SLDPRT
cad/solid_works/Bearing Outer Ring, GT2 Idler Pulley, Configurable.SLDPRT
cad/solid_works/Bearing Seal, GT2 Idler Pulley, Configurable.SLDPRT
cad/solid_works/Body, GT2 Idler Pulley, Configurable.SLDPRT
cad/solid_works/GT2 Idler Pulley with teeth.SLDPRT
cad/solid_works/GT2 Idler Pulley.SLDPRT
cad/solid_works/Heshchen_plungger.SLDPRT
cad/solid_works/Heshchen_solenoid.SLDPRT
cad/solid_works/Limit_Switch.SLDPRT
cad/solid_works/M5_T_Slot nut.SLDPRT
cad/solid_works/NEMA 17 + support.SLDPRT
cad/solid_works/NEMA 17.SLDPRT
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

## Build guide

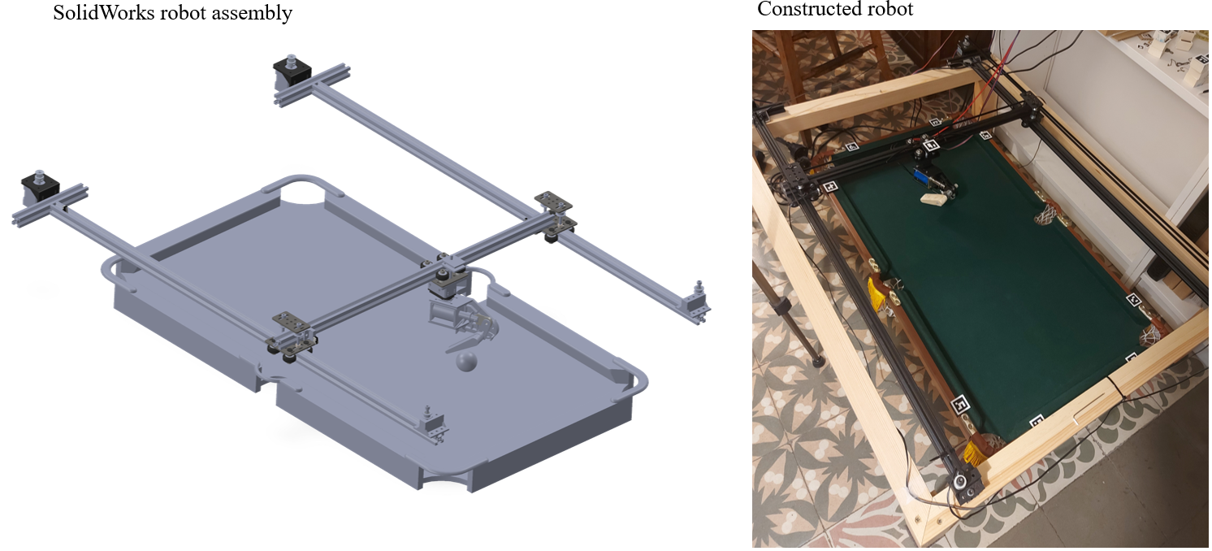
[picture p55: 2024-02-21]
figures/final_assembly.png

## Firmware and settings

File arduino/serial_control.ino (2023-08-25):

//Libraries to include
#include <AccelStepper.h>

//stepper control outputs
#define mot1StepPin 6
#define mot1DirPin 3
#define mot2StepPin 5
#define mot2DirPin 2
#define motMS1Pin 7
#define motMS2Pin 8
#define motMS3Pin 9
#define topSwitch 10
#define bottomSwitch 12
#define leftSwitch 11
#define rightSwitch 13
#define solenoidPin 4

// Define the stepper motor and the pins that is connected to
AccelStepper stepper1(1, mot1StepPin, mot1DirPin); // (Typeof driver: with 2 pins, STEP, DIR)
AccelStepper stepper2(1, mot2StepPin, mot2DirPin);

// Define velocities and accelerations
int calibrationVelocity = 500;
int calibrationAcceleration = 1000;
int workingVelocity = 500;
int workingAcceleration = 1000;

// variables to store calibration positions
int reach_position1;
int reach_position2;

const byte numChars = 64;
char receivedChars[numChars];
char tempChars[numChars];        // temporary array for use when parsing
int sign1 = 1;
int sign2 = 1;
int backup_position = 300;
int infinity = 32766;
int untilTheEnd1 = 0;
int untilTheEnd2 = 0;

boolean newData = false;

// variables to hold the parsed data
int relative_position_stepper1 = 0;
int relative_position_stepper2 = 0;
int mode = -1;
byte microSteps[6] = {
    B000, // full step
    B100, // half step
    B010, // 1/4 step
    B110, // 1/8 step
    B001, // 1/16 step
    B101, // 1/32 step
};

//===============

void setup() {

    Serial.begin(9600);

    // configure initial motor settings
    pinMode(motMS1Pin, OUTPUT);
    pinMode(motMS2Pin, OUTPUT);
    pinMode(motMS3Pin, OUTPUT);

    pinMode(topSwitch, INPUT_PULLUP);
    pinMode(bottomSwitch, INPUT_PULLUP);
    pinMode(leftSwitch, INPUT_PULLUP);
    pinMode(rightSwitch, INPUT_PULLUP);

    pinMode(solenoidPin, OUTPUT);

    digitalWrite(motMS1Pin, LOW);
    digitalWrite(motMS2Pin, LOW);
    digitalWrite(motMS3Pin, LOW);

    delay(200);
    setSpeedAccel(workingVelocity, workingAcceleration);
    Serial.println("<Arduino is ready>");

}

//===============

void loop() {
    recvWithStartEndMarkers();
    
    // every time new data comes, we set the current position of the motors to 0 steps
    // this is because we will move the motors with visual servoing (error vector)
    stepper1.setCurrentPosition(0); 
    stepper2.setCurrentPosition(0);

    if (newData == true) {
        strcpy(tempChars, receivedChars);
            // this temporary copy is necessary to protect the original data
            //   because strtok() used in parseData() replaces the commas with \0
        parseData();
        
        // step mode (includes microstepping option)
        if (mode >= 0) {
            digitalWrite(motMS1Pin, bitRead(microSteps[mode], 2));
            digitalWrite(motMS2Pin, bitRead(microSteps[mode], 1));
            digitalWrite(motMS3Pin, bitRead(microSteps[mode], 0));
            moveSafe();
        }

        // homing
        else if (mode == -1) {
            delay(5000);
            setSpeedAccel(calibrationVelocity, calibrationAcceleration);
            homing();
            setSpeedAccel(workingVelocity, workingAcceleration);
        }

        // calibration mode (find corners)
        else if (mode == -2) {
            delay(5000);
            setSpeedAccel(calibrationVelocity, calibrationAcceleration);
            findMaxPositions();
            setSpeedAccel(workingVelocity, workingAcceleration);
        }

        else if (mode == -3) {
            digitalWrite(solenoidPin, HIGH);      //Switch Solenoid ON
            delay(230);                          //Wait 
            digitalWrite(solenoidPin, LOW);       //Switch Solenoid OFF
            delay(1000); 
        }

    replyToPython();

    }
}

//===============

void setSpeedAccel(int speed, int accel){
    stepper1.setMaxSpeed(speed); // Set maximum speed value for the stepper
    stepper1.setAcceleration(accel); // Set acceleration value for the stepper
    stepper2.setMaxSpeed(speed);
    stepper2.setAcceleration(accel);
}

void positionSigns(int pin){

    // when we touch a limit switch, we need to back off a little bit until 
    // it stops being pressed. For this reason, negative values on limit  
    // switched pins are considered  

    if (pin==leftSwitch || pin==-rightSwitch) {
        sign1=-1;  
        sign2=-1;  
    }
    else if (pin==rightSwitch || pin==-leftSwitch) {
        sign1=1;  
        sign2=1;
    }
    else if (pin==topSwitch || pin==-bottomSwitch) {
        sign1=1;  
        sign2=-1;
    }
    else if (pin==bottomSwitch || pin==-topSwitch) {
        sign1=-1;  
        sign2=1;
    }
}

void reachEnd(int pin) {
    untilTheEnd1=0;
    untilTheEnd2=0;
    stepper1.setCurrentPosition(0);  // Set the current position as zero for now
    stepper2.setCurrentPosition(0);  // Set the current position as zero for now
    positionSigns( pin );
    delay(200);

    stepper1.moveTo(sign1*infinity);  // Set the position to move to
    stepper2.moveTo(sign2*infinity);  // Set the position to move to
    while (digitalRead(pin)) {  // Make the Stepper move CCW until the switch is activated   
        stepper1.run();  // Start moving the stepper
        stepper2.run();  // Start moving the stepper
        untilTheEnd1=untilTheEnd1+sign1;
        untilTheEnd2=untilTheEnd2+sign2;

    }
    stepper1.stop(); // Stop as fast as possible
    stepper2.stop(); // Stop as fast as possible  

    stepper1.setCurrentPosition(0);  // Set the current position as zero for now
    stepper2.setCurrentPosition(0);  // Set the current position as zero for now
    positionSigns( -pin );
    delay(200);

    stepper1.moveTo(sign1*backup_position);  // Set the position to move to
    stepper2.moveTo(sign2*backup_position);  // Set the position to move to
    while (stepper1.currentPosition() != sign1*backup_position || stepper2.currentPosition() != sign2*backup_position) { // Make the Stepper move CW until the switch is deactivated
        stepper1.run();
        stepper2.run();
        untilTheEnd1=untilTheEnd1+sign1;
        untilTheEnd2=untilTheEnd2+sign2;
    }
    
    stepper1.setCurrentPosition(0);  // Set the current position as zero for now
    stepper2.setCurrentPosition(0);  // Set the current position as zero for now
    delay(200);

}

void homing() {

    reachEnd(leftSwitch);
    reachEnd(topSwitch);

    relative_position_stepper1 = 0;
    relative_position_stepper2 = 0;

}

void findMaxPositions() {

    reachEnd(rightSwitch);
    relative_position_stepper1=relative_position_stepper1+untilTheEnd1;
    relative_position_stepper2=relative_position_stepper2+untilTheEnd2;

    reachEnd(bottomSwitch);
    relative_position_stepper1=relative_position_stepper1+untilTheEnd1;
    relative_position_stepper2=relative_position_stepper2+untilTheEnd2;
}

void moveSafe() {
    stepper1.moveTo(relative_position_stepper1);
    stepper2.moveTo(relative_position_stepper2);
    // when we achieved the desired position, we exit the while loop
    while (stepper1.currentPosition() != relative_position_stepper1 || stepper2.currentPosition() != relative_position_stepper2 ) {
        // before running we make sure that switches are not pressed
        if (digitalRead(topSwitch) && digitalRead(bottomSwitch) && digitalRead(leftSwitch) && digitalRead(rightSwitch)){
            stepper1.run();  // Move or step the motor implementing accelerations and decelerations to achieve the target position. Non-blocking function
            stepper2.run();
        }

        else{
            stepper1.stop(); // Stop as fast as possible
            stepper2.stop(); // Stop as fast as possible  
            mode=-1;
            homing();
            break;
        }
    }
}

void parseData() {      // split the data into its parts

    char * strtokIndx; // this is used by strtok() as an index
    strtokIndx = strtok(tempChars,",");      // get the first part - the string
    mode = atoi(strtokIndx);     // convert this part to an integer
    strtokIndx = strtok(NULL, ","); // this continues where the previous call left off
    relative_position_stepper1 = atoi(strtokIndx);     // convert this part to an integer
    strtokIndx = strtok(NULL, ","); // this continues where the previous call left off
    relative_position_stepper2 = atoi(strtokIndx);     // convert this part to an integer
}

void recvWithStartEndMarkers() {
    static boolean recvInProgress = false;
    static byte ndx = 0;
    char startMarker = '<';
    char endMarker = '>';
    char rc;

    while (Serial.available() > 0 && newData == false) {
        rc = Serial.read();

        if (recvInProgress == true) {
            if (rc != endMarker) {
                receivedChars[ndx] = rc;
                ndx++;
                if (ndx >= numChars) {
                    ndx = numChars - 1;
                }
            }
            else {
                receivedChars[ndx] = '\0'; // terminate the string
                recvInProgress = false;
                ndx = 0;
                newData = true;
            }
        }

        else if (rc == startMarker) {
            recvInProgress = true;
        }
    }
}

//===============

void replyToPython() {

    Serial.print("<");
    Serial.print(mode);
    Serial.print(",");
    Serial.print(relative_position_stepper1);
    Serial.print(",");
    Serial.print(relative_position_stepper2);
    Serial.print('>');

        // change the state of the data bool everytime a reply is sent
    newData = false;
}

//===============

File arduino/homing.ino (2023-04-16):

// This is very similar to Example 3 - Receive with start- and end-markers
//    in Serial Input Basics   http://forum.arduino.cc/index.php?topic=396450.0

#include <AccelStepper.h>

//stepper control outputs
#define mot1StepPin 6
#define mot1DirPin 3
#define mot2StepPin 5
#define mot2DirPin 2
#define topSwitch 10
#define bottomSwitch 12
#define leftSwitch 11
#define rightSwitch 13

// Define the stepper motor and the pins that is connected to
AccelStepper stepper1(1, mot1StepPin, mot1DirPin); // (Typeof driver: with 2 pins, STEP, DIR)
AccelStepper stepper2(1, mot2StepPin, mot2DirPin);

int initial_homing1 = -1;
int initial_homing2 = -1;

int pos1 = 1500;
int pos2 = 1500;
int time = 0;

int maxTravel1=5000;
int maxTravel2=5000;

//===============

void setup() {

    Serial.begin(9600);

    pinMode(topSwitch, INPUT_PULLUP);
    pinMode(bottomSwitch, INPUT_PULLUP);
    pinMode(leftSwitch, INPUT_PULLUP);
    pinMode(rightSwitch, INPUT_PULLUP);

    delay(200);
    Serial.println("<Arduino is ready>");
    
    //homing();

}

//===============

void loop() {
    homing_v2();
    // every time new data comes, we set the current position of the motors to 0 steps
    // this is because we will move the motors with visual servoing (error vector)
    stepper1.setCurrentPosition(0); 
    stepper2.setCurrentPosition(0);

    stepper1.moveTo(pos1);
    stepper2.moveTo(pos2);
    // when we achieved the desired position, we exit the while loop
    while (stepper1.currentPosition() != pos1 || stepper2.currentPosition() != pos2 ) {
        // before running we make sure that switches are not pressed
        if (digitalRead(topSwitch) && digitalRead(bottomSwitch) && digitalRead(leftSwitch) && digitalRead(rightSwitch)){
            stepper1.run();  // Move or step the motor implementing accelerations and decelerations to achieve the target position. Non-blocking function
            stepper2.run();
        }

    }   

    pos1=-pos1;
    //pos2=-pos2;
    delay(3000);

}

//===============

void homing() {
    stepper1.setMaxSpeed(400); // Set maximum speed value for the stepper
    stepper1.setAcceleration(700); // Set acceleration value for the stepper
    stepper2.setMaxSpeed(400);
    stepper2.setAcceleration(700);

    while (digitalRead(leftSwitch)) {  // Make the Stepper move CCW until the switch is activated   
        stepper1.moveTo(initial_homing1);  // Set the position to move to
        stepper2.moveTo(initial_homing2);  // Set the position to move to
        initial_homing1--;  // Decrease by 1 for next move if needed
        initial_homing2--;  // Decrease by 1 for next move if needed
        stepper1.run();  // Start moving the stepper
        stepper2.run();  // Start moving the stepper
        delay(time);
    }
    Serial.println("left reached");
    stepper1.setCurrentPosition(0);  // Set the current position as zero for now
    stepper2.setCurrentPosition(0);  // Set the current position as zero for now
    initial_homing1=1;
    initial_homing2=1;
    delay(200);

    //while (!digitalRead(leftSwitch)) { // Make the Stepper move CW until the switch is deactivated
    //    stepper1.moveTo(initial_homing1);  // Set the position to move to
    //    stepper2.moveTo(initial_homing2);  // Set the position to move to
    //    stepper1.run();
    //    stepper2.run();
    //    initial_homing1++;
    //    initial_homing2++;
        //delay(5);
    //}
    for (int i = 0; i <= 200; i++) {
        stepper1.moveTo(initial_homing1);  // Set the position to move to
        stepper2.moveTo(initial_homing2);  // Set the position to move to
        initial_homing1++;  // Decrease by 1 for next move if needed
        initial_homing2++;  // Decrease by 1 for next move if needed
        stepper1.run();  // Start moving the stepper
        stepper2.run();  // Start moving the stepper
        //Serial.println(i);
        delay(time);
    }
    stepper1.setCurrentPosition(0);  // Set the current position as zero for now
    stepper2.setCurrentPosition(0);  // Set the current position as zero for now
    initial_homing1=1;
    initial_homing2=-1;
    delay(200);

    while (digitalRead(topSwitch)) {  // Make the Stepper move CCW until the switch is activated   
        stepper1.moveTo(initial_homing1);  // Set the position to move to
        stepper2.moveTo(initial_homing2);  // Set the position to move to
        initial_homing1++;  // Decrease by 1 for next move if needed
        initial_homing2--;  // Decrease by 1 for next move if needed
        stepper1.run();  // Start moving the stepper
        stepper2.run();  // Start moving the stepper
        delay(time);
    }
    Serial.println("top reached");
    stepper1.setCurrentPosition(0);  // Set the current position as zero for now
    stepper2.setCurrentPosition(0);  // Set the current position as zero for now
    initial_homing1=-1;
    initial_homing2=1;
    delay(200);

    //while (!digitalRead(topSwitch)) { // Make the Stepper move CW until the switch is deactivated
    //    stepper1.moveTo(initial_homing1);  // Set the position to move to
    //    stepper2.moveTo(initial_homing2);  // Set the position to move to
    //    initial_homing1--;
    //    initial_homing2++;
    //    stepper1.run();
    //    stepper2.run();
        //delay(5);
    //}
    for (int i = 0; i <= 200; i++) {
        stepper1.moveTo(initial_homing1);  // Set the position to move to
        stepper2.moveTo(initial_homing2);  // Set the position to move to
        initial_homing1--;  // Decrease by 1 for next move if needed
        initial_homing2++;  // Decrease by 1 for next move if needed
        stepper1.run();  // Start moving the stepper
        stepper2.run();  // Start moving the stepper
        //Serial.println(i);
        delay(time);

    }
    stepper1.setMaxSpeed(600); // Set maximum speed value for the stepper
    stepper1.setAcceleration(800); // Set acceleration value for the stepper
    stepper2.setMaxSpeed(600);
    stepper2.setAcceleration(800);
    delay(200);
}
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

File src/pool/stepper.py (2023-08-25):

from typing import *  # type: ignore

import serial
import serial.tools.list_ports


class Stepper(object):
    """Goes in pair with `serial_control.ino`"""

    def __init__(
        self,
        baudRate       : int           = 9600,
        serialPortName : Optional[str] = None
    ):
        self.connected : bool = True

        if serialPortName is None:
            self.connected : bool = False
            self._automatically_connenct_to_arduino()

        self.startMarker     : str           = '<'
        self.endMarker       : str           = '>'
        self.dataStarted     : bool          = False
        self.dataBuf         : str           = ""
        self.messageComplete : bool          = False
        self.baudRate        : int           = baudRate
        self.serialPortName  : Optional[str] = serialPortName

    def _automatically_connenct_to_arduino(self):
        """Connects to the arduino"""

        # get the first port that has "Arduino" in the name
        for port in self._list_com_ports():
            if "Arduino" in port['name']:
                self.serialPortName = port['device']
                self.connected      = True
                break

    @staticmethod
    def _list_com_ports():
        com_ports = serial.tools.list_ports.comports()
        port_list = []
        
        for port in com_ports:
            port_info = {
                'device': port.device,
                'name'  : port.description
            }
            port_list.append(port_info)
        
        return port_list

    def test_if_connected(self) -> bool:
        """Tests if the arduino is connected"""
        return self.connected

    def waitForArduino(self):

        # wait until the Arduino sends 'Arduino is ready' - allows time for Arduino reset
        # it also ensures that any bytes left over from a previous message are discarded
        
        print("Waiting for Arduino to reset")
        
        msg = ""
        while msg.find("Arduino is ready") == -1:
            msg = self.recvLikeArduino()
            if not (msg == 'XXX'): 
                print(msg)

    def setupSerial(self):

        self.serialPort = serial.Serial(port= self.serialPortName, baudrate = self.baudRate, timeout=0, rtscts=True)

        print("Serial port " + self.serialPortName + " opened  Baudrate " + str(self.baudRate))

        self.waitForArduino()

    def sendToArduino(self,stringToSend):
        assert self.connected, "Arduino is not connected"

        stringWithMarkers = (self.startMarker)
        stringWithMarkers += stringToSend
        stringWithMarkers += (self.endMarker)

        self.serialPort.write(stringWithMarkers.encode('utf-8')) # encode needed for Python3

    def recvLikeArduino(self):

        if self.serialPort.inWaiting() > 0 and self.messageComplete == False:
            x = self.serialPort.read().decode("utf-8") # decode needed for Python3
            
            if self.dataStarted == True:
                if x != self.endMarker:
                    self.dataBuf = self.dataBuf + x
                else:
                    self.dataStarted = False
                    self.messageComplete = True
            elif x == self.startMarker:
                self.dataBuf = ''
                self.dataStarted = True
        
        if (self.messageComplete == True):
            self.messageComplete = False
            return self.dataBuf
        else:
            return "XXX" 

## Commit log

2023-03-29 added arduino libraries
2023-03-30 stepper class to replace py_serial.py
    [serial_control.ino, stepper.py]
2023-03-30 added dslr camera support
2023-04-10 minor fixes and modifications
    [serial_control.ino]
2023-04-10 added lens calibration and updated todo
2023-04-12 micro limit switch test
2023-04-12 added new camera sketch
2023-04-12 moved calibration script
2023-04-13 homing and micro limit switch added
2023-04-15 arduino control: homing and calibration
2023-04-16 arduino control enhanced
2023-04-16 working arduino code
2023-04-17 calibration pixels vs steps
2023-04-19 calibration pixel to step
2023-04-20 calibration proccess is working
    [pixel_step.csv]
2023-04-21 debug calibration pixel to steps
2023-04-21 corrected corner order in wwwarp prespective transform
    [eye.py]
2023-04-21 debugger pixel to step worinkg
    [pixel_step.csv]
2023-04-22 model pixel to step and int positions
    [pixel_step.csv]
2023-04-23 updated offline and online calibration data generation
    [calibration_image_data.csv, calibration_pixel_step.csv, calibration_pixel_to_step.csv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]
2023-04-23 deleted a few files that are not necessary
    [calibration_pixel_step.csv]
2023-04-23 working model and data extraction
    [calibration_pixel_to_step.csv]
2023-04-29 repeatability test added 2
    [repeatability_error.csv, repeatability_image_data.csv]
2023-04-29 refactor: Extracted `Camera.settings` to `Camera_settings`
2023-05-01 updated todo and added solenoid sizing script
2023-05-01 feat: Camera controller has `test_if_any_cameras_are_connected`
2023-05-01 refactor: renamed `Stepper` to `Controller_actuators` and improved it
2023-05-01 refactor: Renamed `Camera` to `Camera_DLSR`
    The logic behind this is that in the future we might incorporate a class like `Camera_webcam`
2023-05-01 refactor: Renamed `Camera_settings` and `stepper.py` file
2023-05-04 new script img processing and print added
2023-05-06 feat: Improved `Camera_DLSR` and `sketch_get_corners.py`
2023-05-07 mechanism kinematics
2023-05-09 mechanism kinematics brute force
2023-05-19 dynamixel velocity profile and solenoid serial
2023-05-27 dynamixel dynamics analysis
    [mod_data_0.csv, mod_data_1.csv, mod_data_2.csv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]
2023-05-27 added dynamixel PID tunning
2023-05-30 added pool frame and minor changes
2023-05-31 first brain release and mod pixel to step
    [calibration_image_data.csv, calibration_pixel_to_step.csv]
2023-06-05 working on fourth case shot and mod fin_X method
2023-06-05 fourth case working
2023-06-06 bug in cbtp shot ball #3
    [brain.py, shot_selection.py]
2023-06-06 solved collision bug adding more ids to row match
    [brain.py, shot_selection.py]
2023-06-07 moved X1 and X2 calculations to error analysis
    [brain.py, error_analysis.py]
2023-06-15 bug regarding size obs_space and size state
    [pool_sim.py]
2023-06-15 bug in variable observation space size
    [pool_sim.py]
2023-06-15 solved bug simplifying the problem
    [random_balls.py]
2023-06-19 refactor: changed pool frame pockets
2023-06-20 add: new enviroments and dataset generation
    [pool_sim_data.csv]
2023-06-20 add: new brute force and generation dataset
    [brute_force_data.csv, pool_sim_data_header.csv]
2023-06-21 added: trying machine learning algorithms
    [brute_force_data.csv, pool_sim_data_header.csv]
2023-06-21 bug: wrong info dict potted balls
    [brute_force_data.csv]
2023-06-21 refactor: moved scripts that don't need data to examples
    [brute_force_data.csv, mod_data_0.csv, mod_data_1.csv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]
2023-06-22 refactor: moving sketches to examples and eye class mod
    [calibration_image_data.csv, calibration_pixel_to_step.csv, repeatability_error.csv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]
2023-06-22 refactor: moving sketches to examples
    [calibration_image_data.csv, calibration_pixel_to_step.csv, repeatability_error.csv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]
2023-06-23 corrected X1 and X2 computation and ehanced green region algorithm
    [error_analysis.py]
2023-06-23 checkpoint before error analysis refactor
    [error_analysis.py]
2023-06-24 refactor: vectorized error analysis class
    [error_analysis.py, utils.py]
2023-06-24 refactor: calibration pixels to steps
    [calibration_image_data.csv, calibration_pixel_to_step.csv]
2023-06-28 added system calibration
    [repeatability_error.csv, repeatability_image_data.csv]
2023-06-28 removed ball detection algorithms from eye (imports were too slow)
    [ball_detection.py, eye.py]
2023-06-28 refactor: stepper calibration using DataExtractor class
2023-06-29 modified system calibration
2023-06-30 fix: corrected flipper angle
    [calibration.py]
2023-07-01 added: analytic camera calibration
2023-07-01 added_ tune offset analytic calibration
2023-07-03 added: new cam calibration and regression model
2023-07-04 added: automatic system calibration
2023-07-04 refactor: get and storage of calibration data
2023-07-04 corrected dynamixel pid write and minor mistakes
    [dynamixel.py, utils.py]
2023-07-04 enhanced data extractors for calibration points (stteper and system)
2023-07-05 added: automatic system calibration analysis
2023-07-05 corrected variable names prespective transform and added comparison scripts
    [eye.py]
2023-07-06 added undist_warp method and corrected analytic system model
    [eye.py]
2023-07-06 added error between ball detection and ground truth + removed preprocessing folder in examples
2023-07-06 added error analysis due to actuator noise
    [error_analysis.py]
2023-07-09 added commputer vision error analysis and enhanced parameters classic cv algorithms
    [ball_detection.py, utils.py]
2023-07-09 enhanced error analysis in cv algorithms and removed some files
    [ball_detection.py]
2023-07-09 added solenoid control
2023-07-10 corrected angles main script
    [brain.py, dynamixel.py]
2023-07-11 corrected angle and debug brain class
    [brain.py]
2023-07-13 updated pool simulation
    [brute_force_data.csv]
2023-07-13 tuned pool frame parameters
2023-07-15 corrected angle actuator CTTP shots
    [brain.py]
2023-07-15 added centroid correction and removed unnecessary conditions
    [brain.py]
2023-07-18 added cad files and updated sys calibration
    [2GT 20B5.SLDPRT, Actuator.SLDASM, GT2 Idler Pulley with teeth.SLDPRT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]
2023-08-25 minor fixes
    [Bearing Ball, GT2 Idler Pulley, Configurable.SLDPRT, Bearing Inner Ring, GT2 Idler Pulley, Configurable.SLDPRT, Bearing Outer Ring, GT2 Idler Pulley, Configura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]
